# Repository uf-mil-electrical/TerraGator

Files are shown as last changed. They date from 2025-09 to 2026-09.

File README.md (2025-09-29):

# TerraGator Rover
This repo should contain all files related to TerraGator ~~ReptileRover~~, including all Electrical, Mechanical (if applicable), and Software files.

Important links
- [TerraGator Team document](https://docs.google.com/document/d/1ea5GAN0c3F9gpOd2iORHwbelWknOrgWVgWwZqf3MmRY/edit?usp=sharing) <br>
- [Russell's brainstorming document for all things TerraGator](https://docs.google.com/document/d/1PND_ZT07X8xPTkg0Q3CSGb8W5NNpszSxxChMyouKteI/edit?usp=sharing)

Thanks!

## Folders
`PCBs` contain PCBs designed for the rover. Deprecated PCBs should be stored in the *Deprecated or Legacy* folder.

`Deprecated or Legacy` contains old documentation, software, CAD, and images.

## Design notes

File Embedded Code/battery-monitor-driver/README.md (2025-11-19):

## Battery Monitor Board Driver

The following code contains the means for operating TerraGator's Battery Monitor Board. The current project structure is listed below:

``` pgssql
battery_monitor/
│
├── CMakeLists.txt
├── pico_sdk_import.cmake
│
├── src/
│   ├── main.c
│   ├── board_config.c / board_config.h
│   ├── drivers/
│   │   ├── current_sens.c / current_sens.h
│   │   ├── led.c / led.h
│   │   ├── rpi5_comm.c / rpi5_comm.h
│   │   ├── sseg.c / sseg.h
│   │   └── voltage_sens.c / voltage_sens.h
│   └── 
└── 
```
For more detailed information on driver, visit [this MILwiki link](https://milwiki.cbrxyz.com/wiki/Battery_Monitor_Board_V1_Driver)

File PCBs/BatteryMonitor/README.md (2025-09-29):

This is where I'd put my BatteryMonitor files.... *if i had any!?!?!?!*

^^About that^^, I've started working on the pcb design for this board. ye. - Russell

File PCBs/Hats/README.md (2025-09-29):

# Pi hat and motor hats super cool

We'll end up with 4 hats (one for the PI, one for each motor driver).

While EN1 and EN2 aren't routed to anything on the Pi-hat, they should still be input/output from the motor hat

# Here's a motor legend
legend for dc hat

# Here's a Pi legend
legend for dc hat

# Here's the general wiring spec (you'll make 4 hats and these will be the connections in-between them)
legend for dc hat

EN1 and EN2 aren't connected to the PI hat but should still be exposed by the hats (just like every other pin)

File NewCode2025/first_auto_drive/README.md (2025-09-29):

# what is this ros pkg

- wheel drivers (topic)
- sonar drivers (topic)
- IMU driver (topic and server)
- main\_node (listener and client)

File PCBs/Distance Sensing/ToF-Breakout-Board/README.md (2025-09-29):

## Overview

The time-of-flight (ToF) breakout board is a small PCB that can be used for collision detection on TerraGator. The plan is to mount one all four sides of TerraGator so that we can minimize collisions between objects and the rover. 

## Documentation

For more information on the ToF sensor used (VL53L1X) and ToF breakout board can be found on the MIL wiki.

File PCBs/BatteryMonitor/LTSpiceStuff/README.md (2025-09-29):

### what does the battery monitor board do???

Not much! It monitors the batteries voltage and will blink an indicator when the 
battery gets too low (so we can change/re-charge it)

It might be worth adding temperature sensors/monitors as a feature in the future.
I don't think overheating is really an issue but idrk.

### what does the battery monitor board look like in LTSpice

A mess!



Here's an image of the LTSpice schematic

#### how it works

- left most thing
    - the leftmost thing is VBat (24V)
    - it's also +5V and -5V (you get them from a buck converter or something)
- second to the left is an op-amp circuit
    - this op-amp has a gain of ~$\frac{5}{24}$
    - this has the annoying side affect of inverting the signal
- inverting stage
    - literally just an op-amp that (un)inverts the signal 
- output stage
    - what should we do???
    - Depends:
        - led indicator
        - digital signal for PI or uP
        - analog voltage that indicates strength of battery

# TODOS

lowk this spice sim assumes that the battery can vary from
0-24V which is 100% cap!

the battery can vary between 22.4V and 24V

22.4V is 0%
24V is 100% 

(and everything in between is linear)

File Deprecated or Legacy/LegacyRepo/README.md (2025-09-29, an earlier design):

Repo for parts for the MIL Rover

Old Rover CAD Screenshot

contact: adammcaleer@ufl.edu

## Project Architecture
Iamge overview

### Finished tasks
Firmware has somewhat shifted away from a build system using wiringPI as a HAL for c++ - have moved towards a build system for assembly and C for performance. <br>
The basics of the drivers for PWM are done under the c_drivers directory, and drivers for an IMU and BME280 are available under the main branch now.<br>
We have now also added configurations for sonar in the form of a kernel interrupt - this being done once again in hopes of better performance<br>
<br>
Our high level software team has finished configuring ROS for our external computer nodes, and have dived into the details of ROS through toturials.<br>
<br>
Additionally, the team has dived into the battery monitor board design, and details of the future voltage dividing procedure.<br>
<br>
The team has also spent a great deal of time researching and buying parts. Included in the documentation directory are details on that procedure, especailly for the motor selection<br>
<br>
We encourage you to explore the repo and read the subdirectory README's and the different available documentation

## Bugs
Firmware bugs are as follows: PWM through DMA drivers needs to become a persistant object to capture memory leaks - otherwise causes issues when run multiple times<br>
Our sonar modules work independently, but need some kind of daisychaning or internal delays to prevent interference with one another.

## Set up to run:
1. Load the gpio_interface module for PWM
```
cd /Mars-Rover/firmware/kernel_modules/
sudo insmod gpio_interface.ko
```

## Installation:
1. Clone our repo
```
git clone https://github.com/kberon/Mars-Rover.git
```
2. Instantiate the kernel modules on start up
```
sudo nano /etc/systemd/system/load_custom_modules.service
```
In that file write:
```
[Unit]
Description=Load Custom Sonar Kernel Modules
After=network.target

[Service]
Type=oneshot
ExecStart=/sbin/insmod /home/raspberry/Mars-Rover/firmware/sonar_1/sonar_1.ko
ExecStart=/sbin/insmod /home/raspberry/Mars-Rover/firmware/sonar_2/sonar_2.ko
ExecStart=/sbin/insmod /home/raspberry/Mars-Rover/firmware/sonar_3/sonar_3.ko
RemainAfterExit=yes

[Install]
WantedBy=multi-user.target
```
Save the file and run the following commands:
```
sudo systemctl daemon-reload
sudo systemctl enable load_custom_modules.service
```

3. For the sensor setup, we will need to install the WiringPi library
```
cd Mars-Rover/firmware/drivers
git clone https://github.com/WiringPi/WiringPi.git
cd WiringPi
./build debian
sudo dpkg -i debian-template/wiringpi_3.10_arm64.deb
```
4. Docker setup
Get the install script:
```
curl -fsSL https://get.docker.com -o get-docker.sh
chmod +x get-docker.sh
```
Remove an existing docker installations with:
```
sudo apt-get purge docker-ce docker-ce-cli containerd.io -y
```
Run the script:
```
./get-docker.sh
```
Fix permissions:
```
sudo usermod -aG docker pi
sudo systemctl unmask docker
sudo chmod 666 /var/run/docker.sock
```
Install docker-compose:
```
pip3 -v install docker-compose
```
Start and reboot Docker:
```
sudo systemctl start docker
sudo init 6
```   
6. To run our camera + sensors executable:
```
sudo apt-get install libgtk-3-dev
sudo apt-get install libopencv-dev
sudo apt install python3-opencv
```

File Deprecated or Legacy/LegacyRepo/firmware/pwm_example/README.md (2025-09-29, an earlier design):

Try running make in this directory.<br>

If it doesn't work/it cannot find the directory then do the following:<br>
**NOTE if any of the below steps fail, go to IF STILL DOESN'T WORK section, do not continue running the next commands NOTE**<br>
cd WiringPi<br>
rm wiringpi_3.2_armhf.deb<br>
./build debian<br>
mv wiringpi_3.2_armhf.deb .<br>
sudo apt install ./wiringpi_3.2_armhf.deb<br>
<br>
<br>
<br>
IF IT STILL DOESN'T WORK<br>
return to firware directory<br>
rm -r WiringPi<br>
git clone https://github.com/WiringPi/WiringPi.git <br>
cd WiringPi<br>
./build debian<br>
mv debian-template/wiringpi_3.2_armhf.deb .<br>
sudo apt install ./wiringpi_3.2_armhf.deb <br>

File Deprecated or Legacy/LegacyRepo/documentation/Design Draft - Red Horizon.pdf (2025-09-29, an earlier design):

### Design Revision CEN3907C: Senior Design for Computer Engineering

Red Horizon Team
Kayleigh Beron, Andrea Chacon, Morgan Cobb, Kayla Dunnuck, Quintin Lopez-Scarim Machine Intelligence Lab - University of Florida

Table of Contents

Introduction
The Red Horizon project aims to develop a prototype of a Mars rover, integrating advanced features to enhance its autonomy and functionality.

Purpose/Need

The purpose of the Red Horizon project lies in providing an educational and research platform for exploring the capabilities of machine intelligence in autonomous robotic systems. This replica serves as a valuable tool for students, researchers, and educators at the Machine Intelligence Lab to study and experiment with autonomous navigation, object detection, and sensor integration. By simulating the functionalities of a Mars rover, the project fulfills the need for practical hands-on experience in developing and deploying intelligent robotic systems.

Red Horizon will be used by the Machine Intelligence Lab to show off the kinds of autonomous projects students of all ages could work on if they choose to pursue STEM and join MIL. However, there are many possible applications as well, as its mechanical chassis design and motor system allow for movement across all kinds of terrains. It’s strong ability to go over things in all kinds of terrain, make it possible to be used in emergency situations, where it could use the camera to detect victims in areas of natural disasters or cramped spaces where it would be too dangerous to send a person without confirmation of victims.

Domain & Prior Art

The Red Horizon project operates within the field of autonomous robotics and control systems. While there have been significant achievements in this domain, including successful Mars rover missions conducted by various countries, our project aims to recreate this to not only help Machine Intelligence Lab bring a stronger attraction to STEM education with something of great historical significance, but to create something that could be applied in emergencies.

Some prior art would be the original Mars Rover that we would be imitating from, as the wheels and mechanical system are nearly identical. As for educational prior art, Makeblock creates “mBots” that are robots that can easily be built and programmed by young teens, to get introduced to the basics of robotics and allow young engineers to both learn and play with the robot they’ve created. The FIRST Competition is also a robotics competition aimed at middle schoolers and high schoolers of different levels to create a robot with autonomous and telemetry modes with computer vision, that allow young kids to learn about the basics of robotics and gain interest.

Differentiation

As for how Red Horizon will be different, Red Horizon will be more complex than those educational tools like FIRST and mBots, as it is a project that wouldn’t be built by the young kids it is aiming to inspire as it would be too difficult for their level. It is a chance for those kids who are working in FIRST Robotics, to see a more complex project and the real world applications of what they could be working on. This is a project we could bring to local schools with FIRST robotics teams and allow them to play with it while seeing how they can apply robotics outside of a high-school competition.

Impact & Risk Assessment

The impact of the Red Horizon project extends primarily to the educational and research domains within the university community. By providing a hands-on learning experience, the project enhances students' understanding of machine intelligence, robotics, and computer engineering.
The project also raises ethical and privacy concerns, particularly regarding the use of onboard cameras for object detection and navigation. The potential for unintended surveillance or privacy breaches requires careful consideration and implementation of privacy safeguards. As for how we will address this, we will ensure that the robot cannot leave MIL room by trying to make a docking station for it, and ensure the camera is at an angle it can only see directly in-front from a low height. The controllers for it will be kept by Dr. Schwartz as well.

Drawbacks and Limitations

While creating a Mars rover replica like Red Horizon for educational purposes is exciting, it comes with several drawbacks and limitations. Firstly, reliance on computer vision for navigation may be prone to errors in identifying colors and shapes accurately, especially in challenging environments. Additionally, the rover's autonomy may lead to unpredictable behavior, potentially causing collisions or getting stuck in obstacles. Moreover, replicating the complex terrain and environmental conditions of Mars accurately can be difficult, limiting the realism and educational value of the experience. Overall however, these limitations shouldn’t be too large to affect the educational experience.

Statement of Work

By the pre-alpha build (03/27) the Red Horizon team plans to have drivers for the Motors and the controller, along with our high level ROS (Robot Operating System) environment. For the drivers we plan to use C++,C, and potentially some assembly for speed and efficiency. C++ and C will be the default for most drivers, and assembly will be used for some reach goal by utilizing some cutting edge communication protocols. For the specific communication protocols we plan to use for each peripheral please see either the tables below, or the diagram included in the systems section. We will use Cmake as our build system since it meshes well with C++, C, assembly, and ROS. The motor board and kill board will be completed and most parts should be ordered and will continue until the end of the alpha build. We also hope to order sonar kits, and to have a better foundational understanding of the current mechanical state of the Red Horizon.

By the completion of our prototype (04/16) development, we hope to have drivers for the gyroscope, camera, and interfacing with our external computer. Once again, we will be utilizing C++,C, and assembly for that, along with Cmake as our build system. The voltage divider board and battery monitor board will be completed and tested to ensure functionality. Some of our secondary features that we hope to get done include drivers for an accelerometer, and patching up any mechanical issues.

As for our alpha build/demo (08/27) we plan to have attached sonar with drivers in C and C++ using Cmake, and hope to utilize daisy-chaining to increase their accuracy. With those sonar attachments come more information that we can use to increase autonomy, which we hope to have at a sufficient level to roam on its own at this point without destroying itself. . Bluetooth and wifi will also be connected to the controllers to the kill board and raspberry pi. LCD output will be created and tested to ensure data from the screen outputs all current data correctly.

Pre-Alpha build

Core features | Done by: | Secondary features | Timeline (Starting March 11th)
Controller Drivers (wifi) | Quintin and Andrea | Order sonar kits/start researching how to daisy chain them | Week 2
Motor/DAC Drivers | Quintin and Andrea | | Week 3
Configure ROS | Morgan | | Week 1-2
Begin teleop code | Morgan and Kayla | | Week 2

Determine the current mechanical state of Red Horizon | Quintin | Week 1
Motor and Kill Board | Kayleigh and Kayla | Weeks 1-3
Initialize Raspberry Pi | Andrea | Weeks 1-3

Prototype

Core features | Done by: | Secondary features | Timeline (Week 4 starting 04/01/2024)
Motors attached with minimal functionality | Everyone | Accelerometer drivers | Weeks 4-6
Gyroscope drivers (I2C) | Quintin | Mechanical fixes | Week 4-5
UI for data/connectivity with computer | Morgan and Kayla | | Week 4
Begin high level data analysis (basic autonomy) | Morgan and Kayla | | Week 5-6
Add camera with base drivers (USB) | Andrea | | Week 6
Configure LCD to Raspberry Pi (SPI) | Andrea | | Week 4-5
Configure remote controller (WIFI) | Andrea and Kayleigh | | Week 5-6
Voltage Divider and Battery Monitor Board | Kayleigh and Kayla | | Week 4-6

Alpha build/demo

Core features | Done by: | Secondary features | Timeline (Continuing on starting 08/12/2024 with some work done over summer)
Attach functioning sonar | Quintin and Andrea | Path mapping with an accelerometer | Week 7-8
Basic autonomy through high level interactions finished | Quintin and Andrea | Mechanical fixes | Week 9-10
Finish part ordering | Kayleigh | | Week 7
Start testing and integration | Everyone | | Week 7-10

Deliverable Artifacts

We intend to deliver the software for the control, as well as drivers/libraries created for the firmware in a github repository. Documentation in the form of jupyter notebooks for these drivers will be provided. Additionally, we will deliver the PCB’s used for the kill board, voltage divider board, motors board, and battery monitor board with their schematics. The final product will be all of these features combined onto the working rover, and delivered to the faculty supervisor, to be used for future research lab demos.

As for how this will be maintained for long-term use there are several plans. The robot will stay in the Machine Intelligence Lab, and the controllers will be kept by Dr. Schwartz. We will provide the CUI to Dr. Schwartz, and keep it on one of the computers in the MIL lab. On one of the computers in the MIL lab, students should just receive the controllers by Dr. Schwartz, run the .exe file on the MIL computer to open the CUI, and once the controllers are connected and the CUI is booted establishing connection to the rover, students should be free to use the rover around the room as pleased. This software will also be available on one of the MIL laptops that can be used at outreach events with local schools for educational purposes, and documentation will be provided on how to use and how to fix some possible issues. Lastly, we will provide a final paper that describes how it works that can be studied by any MIL member.

Mockups
Interfaces

The main interface of this project would be the Bluetooth Logitech Controllers and the LCD Screen. The main inputs from humans come from the kill button (a large physical button on the exterior of the robot to emergency kill), as well as the bluetooth controllers that would change the rover from autonomous to teleop mode (driving by human control) by moving a joystick, and reset it based on a button. We could possibly also try a phone app, not sure if we will implement that yet. The LCD screen would display the status of everything (kill/not kill mode, teleop or autonomous mode, temperature, humidity, altitude, orientation, and if detecting anything on the sensors, all based on the different sensors).
Below is a possible LCD Screen output:

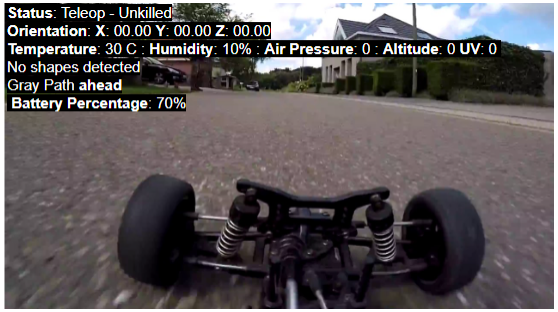
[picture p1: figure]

Figure 1: Potential LCD Screen output Below is a possible remote controller mapping. The soil test is specifically for activating the soil test state that would push a servo stick into the dirt, and output the results from it into the LCD display.

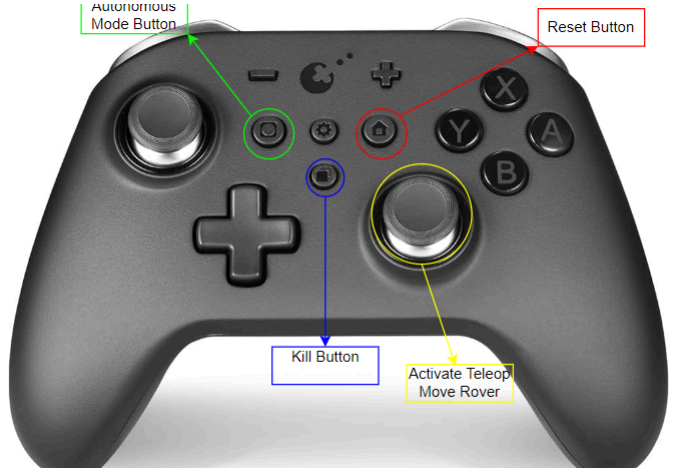
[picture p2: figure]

Figure 2: Remote Controller Map

Systems

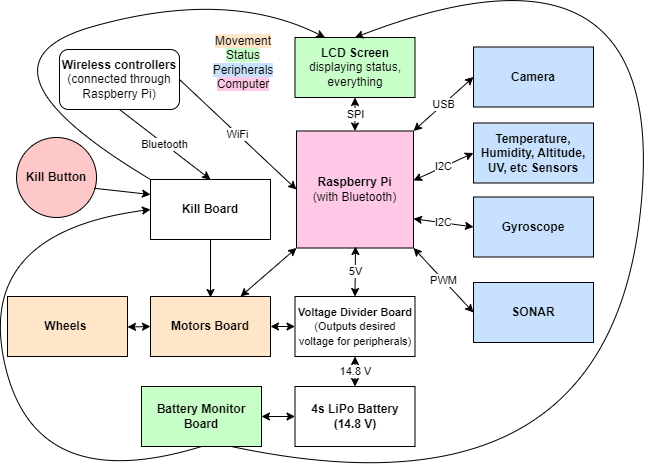
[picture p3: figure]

Above is the general hardware system diagram for our project. Below is the block diagram for the high-level software (computer vision) algorithm. Our main computer will be a Raspberry Pi with Bluetooth functionality that would connect via Bluetooth to the Kill Board (kills all motors/servos when necessary).

We would have a motor system with different motors for each wheel, (possibly mecanum wheels), an arm system involving a servo that just sticks a soil quality sensor into the dirt, and output displayed on the LCD. We would also have a camera connected to the computer searching for shapes and colors (e.g: red circle detected in the distance). Lastly there should be a status system for killed, unkilled, autonomous, teleop, etc.

Networking

There are several necessary communication protocols to fully implement our rover. We would use Serial Peripheral Interface (SPI) communication from our Pi to the screen, to be able to display our sensor and critical information quickly. Additionally, the sensors will use Inter-Integrated Circuits (I2C) or SPI - depending on how critical the data transfers are, as well as the physical location of the hardware components. Additionally, we will use Pulse Width Modulation (PWM) to communicate with the sonar sensors, encoding analog signals into digital signals.

In order to communicate with our Pi from our controller, we will use a CUI that will send instructions to the Pi via Wifi for high data transfer, wide coverage range, and flexibility. We will also use bluetooth or wifi to communicate with the kill board.

Storyboards

The LCD, which is the biggest output, will just look like this most of the time, with the values not in bold, changing every millisecond.

Storyboard example:

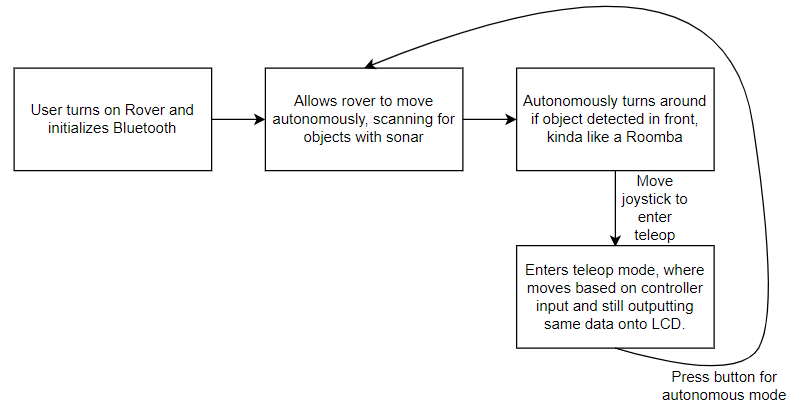
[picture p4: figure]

Draft Schematics

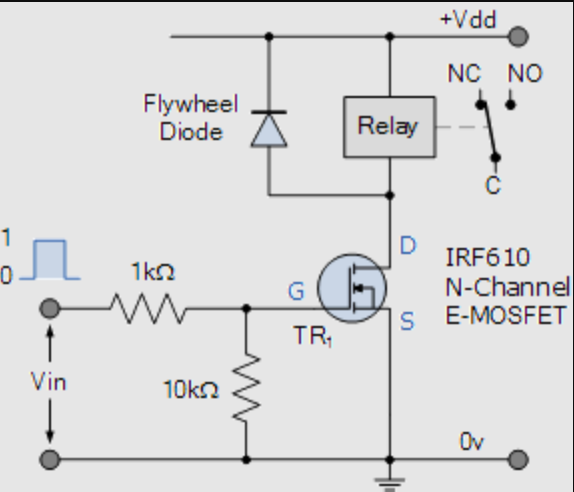
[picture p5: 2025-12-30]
PCBs/Safety Board V0/relay control circuit.png

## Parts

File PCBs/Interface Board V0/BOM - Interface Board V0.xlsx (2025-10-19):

Type | Designator(s) | Qty | Value | Detailed Description | Part Number | Size | Unit Price | Total Price | Vendor
Capacitor | C11, C12, C15, C16, C17, C18, C19, C20, C21, C22, C23, C24, C25, C26, C27, C28, C29, C30, C31, C32 | 20 | 100nF | 0.1 µF ±10% 50V Ceramic Capacitor X7R 0805 (2012 Metric) | C0805C104K5RACTU | 0805 | $0.16 | $3.20 | DigiKey
Capacitor | C1, C2, C6, C7 | 4 | 180uF | 180 µF 50 V Aluminum Electrolytic Capacitors Radial, Can 2000 Hrs @ 105°C | EEU-FC1H181L | 8mm dia | $0.72 | $2.88 | DigiKey
Capacitor | C3, C4, C5, C8, C9, C10 | 6 | 15uF | 15 µF 160 V Aluminum Electrolytic Capacitors Radial, Can 15000 Hrs @ 105°C | 160LLE15MEFC8X11.5 | 8mm dia | $0.52 | $3.12 | DigiKey
Capacitor | C13, C14 | 1 | 0.47uF | 0.47 µF ±10% 50V Ceramic Capacitor X7R 0805 (2012 Metric) | 160LLE15MEFC8X11.5 | 0805 | $0.21 | $0.21 | DigiKey | Total: | $66.32
Connector | X2 | 1 |  | USB-A (USB TYPE-A) Receptacle Connector 4 Position Through Hole, Right Angle | USB-A1HSW6 | 0805 | $0.50 | $0.50 | DigiKey
Connector | X3, X5, X6, X7 | 4 |  | 6 Pin Screw Terminal, Power Tap M3 Through Hole | 7461057 | 0805 | $2.31 | $9.24 | DigiKey
Connector | X4 | 1 |  | 4 Position Wire to Board Terminal Block Horizontal with Board 0.197" (5.00mm) Through Hole | TB001-500-04BE |  | $0.70 | $0.70 | DigiKey
Connector | X8 | 1 |  | 6pin 2.54mm JST |  |  |  | $0.00 | Lab
Connector | X9 | 1 |  | 2pin 2.54mm JST |  |  |  | $0.00 | Lab
Connector | H26 | 1 |  | Connector Header Through Hole, Right Angle 14 position 0.100" (2.54mm) | 22052141 |  | $1.13 | $1.13 | DigiKey
Connector | H25 | 1 |  | 2x14 Headers |  |  |  | $0.00 | Lab
Connector | H1, H21, H22, H23, H24 | 4 |  | Connector Header Through Hole 3 position 0.100" (2.54mm) | 070543-0037 |  | $0.78 | $3.12 | DigiKey
Connector | H18, H19, H20 | 3 |  | Connector Header Through Hole 10 position 0.100" (2.54mm) | BHR-10-VUA |  | $0.28 | $0.84 | DigiKey
Connector | H8, H9, H10, H11, H12, H13, H14, H15, H16, H17 | 10 |  | Connector Header Through Hole 4 position 0.100" (2.54mm) | 70543-0003 |  | $0.85 | $8.50 | DigiKey
Connector | H3, H4, H5, H6, H7 | 5 |  | Connector Header Through Hole 6 position 0.079" (2.00mm) | 35362-0650 |  | $0.35 | $1.75 | DigiKey
Connector | Mount1, Mount2, Mount3, Mount4 | 4 |  | M3 Mounting Bolts |  |  |  | $0.00 | Lab
Connector | X1 | 1 |  | 40 Position Receptacle Connector 0.100" (2.54mm) Through Hole, Right Angle Gold | XG4H-4034 |  | $5.27 | $5.27 | DigiKey
Connector | Radio1 | 1 |  | 16 Position Receptacle Connector 0.100" (2.54mm) Through Hole, Right Angle Gold | 89883-308LF |  | $1.56 | $1.56 | DigiKey
Connector | Mates with 070543-0037 | 4 |  | 3 Rectangular Connectors - Housings Receptacle Black 0.100" (2.54mm) | 50579403 |  | $0.21 | $0.84 | DigiKey
Connector | Mates with 70543-0003 | 10 |  | 4 Rectangular Connectors - Housings Receptacle Black 0.100" (2.54mm) | 50579404 |  | $0.26 | $2.60 | DigiKey
Device | Radio1 | 1 |  | RFDx900 Modem |  |  |  | $0.00 | Lab
Device | X1 | 1 |  | Raspberry Pi 5 |  |  |  | $0.00 | Lab
Diode | D1, D2 | 2 |  | Diode 45 V 6A Surface Mount TO-263AB (D2PAK) | VS-6TQ045S-M3 | TO263AB | $0.76 | $1.52 | DigiKey
Inductor | L1, L2 | 2 | 10uH | 10 µH Shielded Molded Inductor 5 A 43mOhm Max Nonstandard | ASPI-5050LR-100M-T | 6.00mm x 5.70mm | $1.06 | $2.12 | DigiKey
Regulator | U1 | 1 | 5V, 5A | Buck Switching Regulator IC Positive Fixed 5V 1 Output 5A TO-263-8, D2PAK (7 Leads + Tab), TO-263CA | LM2678SX-5.0/NOPB | TO263 | $6.99 | $6.99 | DigiKey
Regulator | U2 | 1 | 3V3, 5A | Buck Switching Regulator IC Positive Fixed 3.3V 1 Output 5A TO-263-8, D2PAK (7 Leads + Tab), TO-263CA | LM2678SX-3.3/NOPB | TO263 | $6.99 | $6.99 | DigiKey
Ribbon cable | Mates with BHR-10-VUA | 3 |  | 10 Position Cable Assembly Rectangular Socket to Socket 0.500' (152.40mm, 6.00") | H3CCH-1006M |  | $1.08 | $3.24 | DigiKey

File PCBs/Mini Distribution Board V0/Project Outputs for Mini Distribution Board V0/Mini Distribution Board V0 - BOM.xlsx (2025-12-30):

Line # | Name | Description | Designator | Quantity | Manufacturer 1 | Manufacturer Part Number 1 | Manufacturer Lifecycle 1 | Supplier 1 | Supplier Part Number 1 | Supplier Unit Price 1 | Supplier Subtotal 1
 | [Cap] SMD Nonpolarized |  | C1, C2 | 2 | Yageo Group | CC0603KRX7R7BB104 | Volume Production | DigiKey | 311-1088-6-ND | 0.006 | 0.06
 | SMD Polarized |  | C3 | 1 | Panasonic | EEE-FK1A681P | Volume Production | DigiKey | PCE3781CT-ND | 0.88 | 0.88
 | SMD Polarized |  | C4 | 1 | Nichicon | UCM0J221MCL1GS | Volume Production | DigiKey | 493-17593-1-ND | 0.47 | 0.47
 | Schottky | Generic | D1 | 1 | Diodes Inc. | B530C-13-F | Volume Production | DigiKey | B530C-FDICT-ND | 0.62 | 0.62
 | [PTC] 500mA Trip | MF-MSMF050-2 | F1 | 1 | Bourns | MF-MSMF050-2 | Volume Production | DigiKey | MF-MSMF050-2DKR-ND | 0.36 | 0.36
 | Right-Angle |  | F2 | 1 | Keystone | 3549-2 | Volume Production | DigiKey | 36-3549-2-ND | 1.23 | 1.23
 | 1x4 Male | 70543-0003 Mates with 005057-9404 | H1, H2 | 2 | Molex | 70543-0003 | Volume Production | Avnet | 0705430003 | 0.42149 | 0.84298
 | 1x2 Male | 0705430036 Mates with 0050579402 | H3, H4 | 2 | Molex | 50-57-9402 | Volume Production | DigiKey | WM2900-ND | 0.31 | 0.62
 | SMD Inductor |  | L1 | 1 | TDK | MLZ2012M330WT000 | Volume Production | DigiKey | 445-6399-1-ND | 0.1 | 0.1
 | 652-MH2029-300Y | 652-MH2029-300Y | L2 | 1 | Bourns | MH2029-300Y | Volume Production | DigiKey | MH2029-300YCT-ND | 0.1 | 0.1
 | PMV48XP | PMV48XP | Q1 | 1 | Nexperia | PMV48XPA2R | Volume Production | DigiKey | 1727-PMV48XPA2RCT-ND | 0.5 | 0.5
 | [Res] SMD Resistor | Generic | R1, R2 | 2 | Yageo Group | RC0603FR-0710KL | Volume Production | DigiKey | 311-10.0KHRDKR-ND | 0.006 | 0.06
 | SPDT |  | S1 | 1 | EAO Switch | 09.03290.01 | Volume Production | DigiKey | 1948-1087-ND | 1.67 | 1.67
 | 3.3V 3A | 3A | U1 | 1 | Texas Instruments | LM2596SX-3.3/NOPB | Volume Production | DigiKey | LM2596SX-3.3/NOPBCT-ND | 6 | 6
 | Comparator | LMV358IDGKR | U2 | 1 | Texas Instruments | LMV358IDGKR | Volume Production | DigiKey | 296-13455-1-ND | 0.38 | 0.38
 | 2pin Screw Terminal |  | X1 | 1 | Same Sky | TB002-500-02BE | Volume Production | DigiKey | 102-6145-ND | 0.4 | 0.4

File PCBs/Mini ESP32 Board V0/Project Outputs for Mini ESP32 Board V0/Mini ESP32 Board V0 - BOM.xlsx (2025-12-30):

Line # | Name | Description | Designator | Quantity | Manufacturer 1 | Manufacturer Part Number 1 | Manufacturer Lifecycle 1 | Supplier 1 | Supplier Part Number 1 | Supplier Unit Price 1 | Supplier Subtotal 1
 | RP-SMA 50-Ohm | PCB.RPSMAFRA.HT | A1 | 1 | Taoglas | PCB.RPSMAFRA.HT | Unknown | DigiKey | 931-1360-ND | 3.59 | 3.59
 | SMD Nonpolarized |  | C1, C2 | 2 | Cal-Chip Electronics | CHV0603N2501R2BCT | Unknown | DigiKey | 4713-CHV0603N2501R2BCT-ND | 0.22 | 0.44
 | [Cap] SMD Nonpolarized |  | C3, C13, C14, C15, C16 | 5 | Yageo Group | CC0603KRX7R7BB104 | Volume Production | DigiKey | 311-1088-6-ND | 0.006 | 0.06
 | SMD Nonpolarized |  | C4, C5 | 2 | Yageo Group | CC0603DRNPO9BN6R0 | Volume Production | DigiKey | 311-1055-1-ND | 0.1 | 0.2
 | SMD Nonpolarized |  | C6, C7, C10, C17, C18 | 5 | Samsung Electro-Mechanics | CL10B105MO8NNWC | Volume Production | DigiKey | 1276-6524-1-ND | 0.006 | 0.06
 | SMD Nonpolarized |  | C8 | 1 | Murata | GRM1885C1H101JA01D | Not Recommended for New Design | DigiKey | 490-1427-1-ND | 0.08 | 0.08
 | SMD Nonpolarized |  | C9 | 1 | TAIYO YUDEN | LMK107BBJ106MALT | Volume Production | DigiKey | 587-3258-1-ND | 0.08 | 0.08
 | SMD Nonpolarized |  | C11, C12 | 2 | KYOCERA AVX | 600S1R8BT250XT4K | Volume Production | DigiKey | 478-600S1R8BT250XT4KCT-ND | 1.38 | 2.76
 | 1x4 Male | 70543-0003 Mates with 005057-9404 | H1 | 1 | Molex | 70543-0003 | Volume Production | Avnet | 0705430003 | 0.42149 | 0.42149
 | 1x3 Male | 070543-0037 Mates with 005057-9403 | H2 | 1 | Molex | 50-57-9403 | Volume Production | DigiKey | WM2901-ND | 0.22 | 0.22
 | SMD Inductor |  | L1 | 1 | Wurth Elektronik | 7447860027G | Unknown | DigiKey | 732-7447860027GCT-ND | 0.1 | 0.1
 | SMD Inductor |  | L2 | 1 | Murata | LQW18AS2N0J00D | Volume Production | DigiKey | 490-LQW18AS2N0J00DCT-ND | 0.11 | 0.11
 | 652-MH2029-300Y | 652-MH2029-300Y | L3 | 1 | Bourns | MH2029-300Y | Volume Production | DigiKey | MH2029-300YCT-ND | 0.1 | 0.1
 | [Res] SMD Resistor | Generic | R1, R2 | 2 | Vishay | MCT06030C2709FP500 | Volume Production | DigiKey | 749-1631-1-ND | 0.1 | 0.2
 | [Res] SMD Resistor | Generic | R3, R4 | 2 | Yageo Group | RC0603FR-075K1L | Volume Production | DigiKey | 311-5.10KHRDKR-ND | 0.007 | 0.07
 | [Res] SMD Resistor | Generic | R5 | 1 | Yageo Group | RT0603BRD071ML | Volume Production | DigiKey | YAG4498CT-ND | 0.1 | 0.1
 | [Res] SMD Resistor | Generic | R6, R7 | 2 | Yageo Group | RC0603FR-0710KL | Volume Production | DigiKey | 311-10.0KHRCT-ND | 0.006 | 0.06
 | [Res] SMD Resistor | Generic | R8, R9 | 2 | Panasonic | ERA3ARB202V | Volume Production | DigiKey | P2.0KBDCT-ND | 0.35 | 0.7
 | ESP32-S2FN4R2 |  | U1 | 1 | Espressif Systems | ESP32-S2FN4R2 | Unknown | DigiKey | 1965-ESP32-S2FN4R2CT-ND | 2.94 | 2.94
 | W25Q128JVS | W25Q128JVSIQ TR | U2 | 1 | Winbond | W25Q128JVSIQ TR | Unknown | DigiKey | 256-W25Q128JVSIQTRCT-ND | 2.13 | 2.13
 | USB-C |  | X1 | 1 | JAE Electronics | DX07S024JA1R1300 | Volume Production | DigiKey | 670-3104-1-ND | 2.1 | 2.1
 | 40MHz Crystal | CX2016DB40000D0FLJCC | Y1 | 1 | KYOCERA AVX | CX2016DB40000D0FLJCC | Unknown | DigiKey | 478-CX2016DB40000D0FLJCCDKR-ND | 0.84 | 0.84

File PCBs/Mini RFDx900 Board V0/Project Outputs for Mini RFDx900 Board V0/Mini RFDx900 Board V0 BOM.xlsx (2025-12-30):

Line # | Name | Description | Designator | Quantity | Manufacturer 1 | Manufacturer Part Number 1 | Manufacturer Lifecycle 1 | Supplier 1 | Supplier Part Number 1 | Supplier Unit Price 1 | Supplier Subtotal 1
 | [Cap] SMD Nonpolarized |  | C1, C2, C3 | 3 | Yageo Group | CC0603KRX7R7BB104 | Volume Production | DigiKey | 311-1088-6-ND | 0.006 | 0.06
 | SMD LED | Generic | D1, D2 | 2 | Harvatek | B1701UY--20D000214U1930 | Unknown | DigiKey | 3147-B1701UY--20D000214U1930CT-ND | 0.1 | 0.2
 | 1x2 Male | 0705430036 Mates with 0050579402 | H1 | 1 | Molex | 50-57-9402 | Volume Production | DigiKey | WM2900-ND | 0.31 | 0.31
 | 652-MH2029-300Y | 652-MH2029-300Y | L1 | 1 | Bourns | MH2029-300Y | Volume Production | DigiKey | MH2029-300YCT-ND | 0.1 | 0.1
 | [XOSC] SMD 12MHz |  | O1 | 1 | Murata | CSTNE12M0GH5L000R0 | Volume Production | DigiKey | 490-17947-1-ND | 0.32 | 0.32
 | [Res] SMD Resistor | Generic | R1, R2 | 2 | Stackpole Electronics | RMCF0603FT1K00 | Volume Production | DigiKey | RMCF0603FT1K00DKR-ND | 0.007 | 0.07
 | [Res] SMD Resistor | Generic | R3 | 1 | Yageo Group | RC0603FR-0710KL | Volume Production | DigiKey | 311-10.0KHRDKR-ND | 0.1 | 0.1
 | [Res] SMD Resistor | Generic | R4, R5 | 2 | Vishay | MCT06030C2709FP500 | Volume Production | DigiKey | 749-1631-1-ND | 0.1 | 0.2
 | [Res] SMD Resistor | Generic | R6, R7 | 2 | Yageo Group | RC0603FR-075K1L | Volume Production | DigiKey | 311-5.10KHRDKR-ND | 0.007 | 0.07
 | RFDX900 | RFDX900 Long-Range RF Module | Radio1 | 1 | Amphenol Communications Solutions | 71609-308LF | Volume Production | DigiKey | 609-71609-308LF-ND | 2.71 | 2.71
 | USB-UART Bridge | MCP2200T-I/SO | U1 | 1 | Microchip | MCP2200T-I/SO | Volume Production | DigiKey | MCP2200T-I/SOCT-ND | 2.61 | 2.61
 | USB-C |  | X1 | 1 | JAE Electronics | DX07S024JA1R1300 | Volume Production | DigiKey | 670-3104-1-ND | 2.1 | 2.1

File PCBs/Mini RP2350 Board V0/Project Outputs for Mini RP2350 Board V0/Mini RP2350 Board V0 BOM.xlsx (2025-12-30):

Line # | Name | Description | Designator | Quantity | Manufacturer 1 | Manufacturer Part Number 1 | Manufacturer Lifecycle 1 | Supplier 1 | Supplier Part Number 1 | Supplier Unit Price 1 | Supplier Subtotal 1
 | [Cap] SMD Nonpolarized |  | C1, C4, C5, C6, C7, C8, C9, C10, C11, C15, C16, C17, C18, C19, C21, C22, C23, C24, C25, C26, C27 | 21 | Yageo Group | CC0603KRX7R7BB104 | Volume Production | DigiKey | 311-1088-6-ND | 0.006 | 0.126
 | [Cap] SMD Nonpolarized |  | C2, C3 | 2 | Murata | GCM1885C2A150FA16D | Volume Production | DigiKey | 490-16416-1-ND | 0.14 | 0.28
 | [Cap] SMD Nonpolarized |  | C12, C13, C14, C20 | 4 | Murata | GRM188R61E475KE11D | Volume Production | DigiKey | 490-7203-1-ND | 0.08 | 0.32
 | SMD LED | Generic | D1 | 1 | Osram Opto | LG R971-KN-1-0-20-R18 | Unknown | DigiKey | 475-LGR971-KN-1CT-ND | 0.15 | 0.15
 | SMD LED | Generic | D2 | 1 | Osram | LY R976-PS-36-0-20-R18 | Unknown | DigiKey | 475-LYR976-PS-36-0-20-R18CT-ND | 0.15 | 0.15
 | SMD LED | Generic | D3 | 1 | Osram Opto | LS R976-NR-1-0-20-R18 | Unknown | DigiKey | 475-LSR976-NR-1CT-ND | 0.15 | 0.15
 | SMD LED | Generic | D4, D5 | 2 | Wurth Elektronik | 150080BS75000 | Unknown | DigiKey | 732-4982-1-ND | 0.19 | 0.38
 | 2x5 Shrouded | BHR-10-VUA | H1, H2, H3 | 3 | Adam Tech | BHR-10-VUA | Volume Production | DigiKey | 2057-BHR-10-VUA-ND | 0.28 | 0.84
 | 1x3 Male | 070543-0037 Mates with 005057-9403 | H4, H6, H7, H8, H10 | 5 | Molex | 50-57-9403 | Volume Production | DigiKey | WM2901-ND | 0.22 | 1.1
 | 1x2 Male | 0705430036 Mates with 0050579402 | H5 | 1 | Molex | 50-57-9402 | Volume Production | DigiKey | WM2900-ND | 0.31 | 0.31
 | [Header] Shrouded 1x6 Male | 0705430005 Mates with 0050579406 | H9, H12 | 2 | Molex | 50-57-9406 | Volume Production | DigiKey | WM2904-ND | 0.4 | 0.8
 | 1x4 Male | 70543-0003 Mates with 005057-9404 | H11 | 1 | Molex | 70543-0003 | Volume Production | Avnet | 0705430003 | 0.42149 | 0.42149
 | 652-MH2029-300Y | 652-MH2029-300Y | L1 | 1 | Bourns | MH2029-300Y | Volume Production | DigiKey | MH2029-300YCT-ND | 0.1 | 0.1
 | SMD Inductor |  | L2 | 1 | Pulse Electronics | BSCY00160808100MCP | Volume Production | DigiKey | 553-BSCY00160808100MCPCT-ND | 0.1 | 0.1
 | [Res] SMD Resistor | Generic | R1, R2 | 2 | Vishay | MCT06030C2709FP500 | Volume Production | DigiKey | 749-1631-1-ND | 0.1 | 0.2
 | [Res] SMD Resistor | Generic | R3, R8, R10, R12, R13, R14, R15, R16 | 8 | Stackpole Electronics | RMCF0603FT1K00 | Volume Production | DigiKey | RMCF0603FT1K00DKR-ND | 0.007 | 0.07
 | [Res] SMD Resistor | Generic | R4, R5 | 2 | Yageo Group | RC0603FR-075K1L | Volume Production | DigiKey | 311-5.10KHRDKR-ND | 0.007 | 0.07
 | [Res] SMD Resistor | Generic | R6 | 1 | Susumu | RR0816Q-330-D | Not Recommended for New Design | DigiKey | RR08Q33DCT-ND | 0.1 | 0.1
 | [Res] SMD Resistor | Generic | R7, R9, R11, R17 | 4 | Panasonic | ERA3ARB202V | Volume Production | DigiKey | P2.0KBDCT-ND | 0.35 | 1.4
 | Standard pushbutton |  | S1, S2 | 2 | TE Connectivity | 1825910-6 | Volume Production | DigiKey | 450-1650-ND | 0.13 | 0.26
 | W25Q128JVS | W25Q128JVSIQ TR | U1 | 1 | Winbond | W25Q128JVSIQ TR | Unknown | DigiKey | 256-W25Q128JVSIQTRCT-ND | 2.13 | 2.13
 | RP2350B | QFN-80 Package | U2 | 1 | Raspberry Pi | SC1510-A4 | Unknown | DigiKey | 2648-SC1510-A4CT-ND | 1 | 1
 | [IC] Level Shifter (2) | TXS0108EQPWRQ1 | U3 | 1 | Texas Instruments | TXS0108EQPWRQ1 | Volume Production | DigiKey | 296-42401-1-ND | 2.05 | 2.05
 | USB-C |  | X1 | 1 | JAE Electronics | DX07S024JA1R1300 | Volume Production | DigiKey | 670-3104-1-ND | 2.1 | 2.1
 | 12MHz | 815-ABM8-272-T3 | Y1 | 1 | Abracon | ABM8-272-T3 | Volume Production | DigiKey | 535-ABM8-272-T3CT-ND | 0.66 | 0.66

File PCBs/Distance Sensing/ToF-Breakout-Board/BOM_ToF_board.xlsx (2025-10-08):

Country of Origin may be different at time of shipment.
The HTSUS and ECCN information shown is for informational purposes only and is not a representation or warranty as to the accuracy or reliability of these classifications. All information is provided "as is" and is subject to change without notice. Any use made of the information provided is without recourse to Digi-Key and at the user's risk.
Index | Designator | Manufacturer Part Number | Manufacturer Name | Description | Lead Time | Availability | Stock Status | Attrition % | Requested Quantity 1 | Pack Quantity 1 | Pack Type 1 | Digi-Key Part Number 1 | Unit Price 1 | Extended Price 1 | Minimum Order Quantity 1 | Customer Reference | Requested Part Number | Lead Weeks | Datasheet | Reference Designator | US Import Tariff | Note | Part Status | RoHS Status | Moisture Sensitivity Level (MSL) | ECCN | HTSUS | Country of Origin | Environmental Information | Original Part numbers | Image | Product Notes
1 | D1 | 150060YS75000 | Würth Elektronik | LED YELLOW CLEAR 0603 SMD |  | 85,434 | In Stock |  | 7 | 7 | Cut Tape (CT) | 732-4981-1-ND | 0.15000 | $1.05 | 1 |  | 732-4981-2-ND | 11 | https://www.we-online.com/components/products/datasheet/150060YS75000.pdf |  | May apply on shipments to the U.S. |  | Active | ROHS3 Compliant | 3 (168 Hours) | EAR99 | 8541.41.0000 | China | https://mm.digikey.com/Volume0/opasdata/d220001/medias/docus/744/Certificate_of_Compliance_ROHS.pdf | 732-4981-2-ND | https://mm.digikey.com/Volume0/opasdata/d220001/medias/images/2958/WL-SMCW%20Series%200603.jpg
2 | R1 | RC0603FR-07220RL | YAGEO | RES 220 OHM 1% 1/10W 0603 |  | 313,724 | In Stock |  | 10 | 10 | Cut Tape (CT) | 311-220HRCT-ND | 0.00900 | $0.09 | 1 |  | 311-220HRTR-ND | 18 | https://www.yageogroup.com/content/datasheet/asset/file/PYU-RC_GROUP_51_ROHS_L |  | N/A |  | Active | ROHS3 Compliant | 1 (Unlimited) | EAR99 | 8533.21.0030 | Taiwan | https://www.yageo.com/en/Download/Index/certificates#rchip | 311-220HRTR-ND | https://mm.digikey.com/Volume0/opasdata/d220001/medias/images/4322/cut-tape-render.jpg
3 | R2 | RC0603FR-0710KL | YAGEO | RES 10K OHM 1% 1/10W 0603 |  | 15,705,619 | In Stock |  | 10 | 10 | Cut Tape (CT) | 311-10.0KHRCT-ND | 0.00900 | $0.09 | 1 |  | 311-10.0KHRCT-ND | 18 | https://www.yageogroup.com/content/datasheet/asset/file/PYU-RC_GROUP_51_ROHS_L |  | N/A |  | Active | ROHS3 Compliant | 1 (Unlimited) | EAR99 | 8533.21.0030 | Taiwan | https://www.yageo.com/en/Download/Index/certificates#rchip | 311-10.0KHRCT-ND | https://mm.digikey.com/Volume0/opasdata/d220001/medias/images/4322/cut-tape-render.jpg
4 | C1, C2 | C0603C104K5RACTU | KEMET | CAP CER 0.1UF 50V X7R 0603 |  | 7,063,446 | In Stock |  | 20 | 20 | Cut Tape (CT) | 399-C0603C104K5RACTUCT-ND | 0.01100 | $0.22 | 1 |  | 399-C0603C104K5RACTUCT-ND | 15 | https://search.kemet.com/download/datasheet/C0603C104K5RAC7867 |  | May apply on shipments to the U.S. |  | Active | ROHS3 Compliant | 1 (Unlimited) | EAR99 | 8532.24.0020 | China |  | 399-C0603C104K5RACTUCT-ND | https://mm.digikey.com/Volume0/opasdata/d220001/medias/images/4322/cut-tape-render.jpg
5 | C3 | GRM188R61E475KE11D | Murata Electronics | CAP CER 4.7UF 25V X5R 0603 |  | 562,884 | In Stock |  | 10 | 10 | Cut Tape (CT) | 490-7203-1-ND | 0.03600 | $0.36 | 1 |  | 490-7203-1-ND | 12 | https://search.murata.co.jp/Ceramy/image/img/A01X/G101/ENG/GRM188R61E475KE11-01.pdf |  | N/A |  | Active | ROHS3 Compliant | 1 (Unlimited) | EAR99 | 8532.24.0020 | Japan |  | 490-7203-1-ND | https://mm.digikey.com/Volume0/opasdata/d220001/medias/images/4322/cut-tape-render.jpg
6 | U1 | VL53L1CXV0FY/1 | STMicroelectronics | SENSOR OPTICAL 0-62CM I2C |  | 13,004 | In Stock |  | 7 | 7 | Cut Tape (CT) | 497-17764-1-ND | 5.18400 | $36.29 | 1 |  | 497-17764-1-ND | 16 | https://www.st.com/resource/en/datasheet/vl53l1x.pdf |  | May apply on shipments to the U.S. |  | Active | ROHS3 Compliant | 3 (168 Hours) | EAR99 | 9031.80.8085 | China |  | 497-17764-1-ND | https://mm.digikey.com/Volume0/opasdata/d220001/medias/images/2878/MFG_VL53L1CXV0FY%5E1.jpg

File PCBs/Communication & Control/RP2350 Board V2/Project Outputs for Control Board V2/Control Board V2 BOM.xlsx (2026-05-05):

 | Bill of Materials
Project Name: | Control Board V2.PrjPcb
Part Number | Designator | Manufacture | Manufacture Part Number | Supplier | Supplier Part Number | Supplier Unit Price | Quantity
[LED] SMD 0805 Green | D1 | Osram Opto | LG R971-KN-1-0-20-R18 | DigiKey | 475-LGR971-KN-1CT-ND | $0.15 | 1
[LED] SMD 0805 Yellow | D2 | Osram | LY R976-PS-36-0-20-R18 | DigiKey | 475-LYR976-PS-36-0-20-R18CT-ND | $0.15 | 1
[LED] SMD 0805 Red | D3 | Osram Opto | LS R976-NR-1-0-20-R18 | DigiKey | 475-LSR976-NR-1CT-ND | $0.15 | 1
[LED] SMD 0805 Blue | D4, D5 | Wurth Elektronik | 150080BS75000 | DigiKey | 732-4982-1-ND | $0.19 | 2
[Header] Shrouded 2x5 Male | H1, H2, H3 | Adam Tech | BHR-10-VUA | DigiKey | 2057-BHR-10-VUA-ND | $0.28 | 3
[Header] Shrouded 1x3 Male | H4, H5, H6, H7, H8, H9, H10, H12, H13, H14 | Molex | 70543-0037 | DigiKey | WM4825-ND | $0.78 | 10
[Header] Shrouded 1x2 Male | H11 | Molex | 70543-0036 | DigiKey | WM4824-ND | $0.92 | 1
[Header] Shrouded 1x6 Male | H15 | Molex | 70543-0005 | DigiKey | WM4804-ND | $1.15 | 1
[Ferrite] SMD 0805 3A 30ohm | L1 | Bourns | MH2029-300Y | DigiKey | MH2029-300YCT-ND | $0.10 | 1
[220] SMD 0603 1% 1/10W | R1, R2, R3 | TE Connectivity | CRGCQ0805F220R | DigiKey | A129741CT-ND | $0.14 | 3
[1k] SMD 0603 1% 1/10W | R4, R5 | Stackpole Electronics | RMCF0603FT1K00 | DigiKey | RMCF0603FT1K00DKR-ND | $0.01 | 2
[Level Shifter] MC14504BDTR2G Breakout | X1 | onsemi | MC14504BDTR2G | DigiKey | MC14504BDTR2GOSCT-ND | $0.66 | 1
[Pi] RP2350B Breakout | X2 |  |  |  |  |  | 1
[Screw Terminal] 3pin | X4 | Same Sky | TB003-500-P03BE | DigiKey | 102-6162-ND | $0.62 | 1
 |  |  |  |  |  | $5.30 | 29
Notes

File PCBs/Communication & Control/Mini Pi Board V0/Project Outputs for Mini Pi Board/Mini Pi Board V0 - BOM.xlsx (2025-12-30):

Line # | Name | Description | Designator | Quantity | Manufacturer 1 | Manufacturer Part Number 1 | Manufacturer Lifecycle 1 | Supplier 1 | Supplier Part Number 1 | Supplier Unit Price 1 | Supplier Subtotal 1
 | SMD LED | Generic | D1 | 1 | Osram Opto | LG R971-KN-1-0-20-R18 | Unknown | DigiKey | 475-LGR971-KN-1CT-ND | 0.15 | 0.15
 | SMD LED | Generic | D2 | 1 | Osram | LY R976-PS-36-0-20-R18 | Unknown | DigiKey | 475-LYR976-PS-36-0-20-R18CT-ND | 0.15 | 0.15
 | SMD LED | Generic | D3 | 1 | Osram Opto | LS R976-NR-1-0-20-R18 | Unknown | DigiKey | 475-LSR976-NR-1CT-ND | 0.15 | 0.15
 | 1x3 Male | 070543-0037 Mates with 005057-9403 | H1 | 1 | Molex | 50-57-9403 | Volume Production | DigiKey | WM2901-ND | 0.22 | 0.22
 | 652-MH2029-300Y | 652-MH2029-300Y | L1 | 1 | Bourns | MH2029-300Y | Volume Production | DigiKey | MH2029-300YCT-ND | 0.1 | 0.1
 | [Res] SMD Resistor | Generic | R1, R2, R3 | 3 | Stackpole Electronics | RMCF0603FT1K00 | Volume Production | DigiKey | RMCF0603FT1K00DKR-ND | 0.007 | 0.07
 | Raspberry Pi 5 | Raspberry Pi 5 | X1 | 1 | Omron | XG4H-4034 | Volume Production | DigiKey | XG4H-4034-ND | 5.16 | 5.16
 | 4pin Screw Terminal |  | X2 | 1 | Same Sky | TB002-500-04BE | Volume Production | DigiKey | 102-6147-ND | 0.77 | 0.77

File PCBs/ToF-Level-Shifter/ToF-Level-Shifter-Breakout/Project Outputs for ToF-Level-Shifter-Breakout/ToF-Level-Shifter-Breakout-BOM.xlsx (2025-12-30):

Comment | Description | Designator | Footprint | LibRef | Quantity | DigiKey link
Cap | 4.7uF 0603 ceramic cap | C4 | CAPC0603 | Cap | 1 | https://www.digikey.com/en/products/detail/samsung-electro-mechanics/CL10A475KO8NNNC/3887442
Cap | 0.1uF 0603 ceramic cap | C1, C2, C3 | CAPC0603 | Cap | 3 | https://www.digikey.com/en/products/detail/samsung-electro-mechanics/CL10F104ZB8NNNC/3886670
1x4 0.1in Header |  | P1 | 1x4 0.1in Header | 1x4 0.1in Header | 0 | Just use a standard 2.54mm pitch header
Header 7 | Header, 7-Pin | P2 | HDR1X7 | Header 7 | 0 | ^
Res | 300kohm RES 0603 | R2 | RES0603 | Res | 1 | https://www.digikey.com/en/products/detail/rohm-semiconductor/ESR03EZPJ304/4051237
Res | 200kohm RES 0603 | R1 | RES0603 | Res | 1 | https://www.digikey.com/en/products/detail/rohm-semiconductor/ESR03EZPJ204/4051216
Res | 10kohm RES0603 | R3, R4, R5, R6, R7 | RES0603 | Res | 5 | https://www.digikey.com/en/products/detail/rohm-semiconductor/ESR03EZPF1002/1983429
ADPL40502AUJZ-1.8-R7 | Low Noise, 200mA, CMOS Linear Regulator (LDO) | U1 | TSOT-23-5_UJ-5_ADI | ADPL40502AUJZ-1.8-R7 | 1 | https://www.digikey.com/en/products/detail/analog-devices-inc/ADPL40502AUJZ-1-8-R7/26262777
PCA9306DCTR | 2-bit bidirectional 400-kHz I2C/SMBus voltage level translator | U2 | SOP65P400X130-8N | PCA9306DCTR | 1 | https://www.digikey.com/en/products/detail/texas-instruments/PCA9306DCTR/809792
VL53L1CXV0FY/1 | ToF Optical Sensor 157.480 (4m) I²C Output from STMelectronics | U3 | LGA-12 (VL53L1CXV0FY/1) | VL53L1CXV0FY/1 | 0 | Use ones that have already been ordered
DigiKey Link: https://www.digikey.com/en/mylists/list/5HL9NZVCED |  |  |  |  | 13
Collaborator PW: MIL2025!

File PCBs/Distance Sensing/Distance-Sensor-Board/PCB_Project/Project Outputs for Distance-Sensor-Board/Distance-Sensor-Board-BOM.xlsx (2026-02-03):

Added to List? | Comment | Description | Designator | Footprint | LibRef | Quantity | DigiKey Link | Notes
TRUE | BOOT | SWITCH TACTILE SPST-NO 0.05A 24V | B1, B2 | SPST-PUSH-BUTTON | 1825910-6 | 2 | https://www.digikey.com/en/products/detail/te-connectivity-alcoswitch-switches/1825910-6/1632536
TRUE | 10uF | 10uF electrolytic cap, radial can, SMD | C1, C2 | RADIAL_CAN_CAP_4_X_5.8_SMD | EEE-FK1E100R | 2 | https://www.digikey.com/en/products/detail/panasonic-electronic-components/EEE-FK1E100R/765964
TRUE | Cap | 4.7uF ceramic cap | C4, C5, C6, C10 | CAP0603 | Cap | 4 | https://www.digikey.com/en/products/detail/samsung-electro-mechanics/CL10A475KO8NNNC/3887442
TRUE | Cap | 100pF ceramic cap | C38 | CAP0603 | Cap | 1 | https://www.digikey.com/en/products/detail/murata-electronics/GRM0335C1E101JA01D/702426
TRUE | Cap | 1uF ceramic cap | C25, C26 | CAP0603 | Cap | 2 | https://www.digikey.com/en/products/detail/samsung-electro-mechanics/CL10B105MO8NNWC/5961008
TRUE | Cap | 100nF ceramic cap | C3, C7, C8, C9, C11, C12, C13, C14, C15, C16, C17, C18, C19, C20, C21, C22, C23, C24, C27, C28, C29, C30, C31, C32, C33, C34, C35, C36, C37 | CAPC0603 | Cap | 29 | https://www.digikey.com/en/products/detail/samsung-electro-mechanics/CL10F104ZB8NNNC/3886670
TRUE | MF-MSMF050-2 | [Fuse] Polymeric PTC Resettable Fuse 15V 500 mA Ih Surface Mount 1812 (4532 Metric), Concave | F1 | FUSM4632X85 | MF-MSMF050-2 | 1 | https://www.digikey.com/en/products/detail/bourns-inc/MF-MSMF050-2/662816
TRUE | MH2029-300Y | [Inductor] FB 0805 | FB1 | L0805 | MH2029-300Y | 1 | https://www.digikey.com/en/products/detail/bourns-inc/MH2029-300Y/2563323
TRUE | USB-B | USB-B (USB TYPE-B) USB 2.0 Receptacle Connector 4 Position Through Hole, Right Angle | J1 | SAMTEC_USB-B-S-X-X-TH | USB-B-S-X-X-TH | 1 | https://www.digikey.com/en/products/detail/samtec-inc/USB-B-S-F-B-TH/2686101
FALSE | Thru-Hole Jumper | Clip Jumper | J2, J4 | [Jumper] Solderable Jumper | [Jump] Thru-Hole 2pin | 2 |  | Just pads on PCB
TRUE | [Connector] 879142016 | 2x10 2.54mm pitch header | J3 | [Connector] CONN20 | [Connector] 879142016 | 1 | Just pads and standard header
TRUE | 3.3uH | Power Inductors - SMD IND 3.3uH used for RP2350 VREG | L1 | 2016_SMD_Inductor | INDUCTOR 3.3uH | 1 | https://www.digikey.com/en/products/detail/abracon-llc/AOTA-B201610S3R3-101-T/25621527
TRUE | 2 port screw | 2 Position Wire to Board Terminal Block Horizontal with Board 0.200 (5.08mm) Through Hole | P1 | [CONNECTOR] 5MM_2PORT_SCREW | [Connector] 691213510002 | 1 | https://www.digikey.com/en/products/detail/w%C3%BCrth-elektronik/691213510002/11477374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
TRUE | UART | Header, Molex, 2mm Pitch Sherlock Header, Single Row, Right Angle 3 Circuits, Length 3.3mm | P2 | MOLEX-HDR-1X3-SHERLOCK-RA | MOLEX-HDR-1x3-SHERLOCK_RA | 1 | https://www.digikey.com/en/products/detail/molex/0353630360/755311?gclsrc=aw.ds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
TRUE | FDN340P | [MOSFET-P] P-Channel 20 V 2A (Ta) 500mW (Ta) Surface Mount SOT-23-3 | Q1 | SOT95P240X120-3N | [PMOS] FDN340P | 1 | https://www.digikey.com/en/products/detail/onsemi/FDN340P/965304
TRUE | Res | 33 ohm res | R1 | RES0603 | Res | 1 | https://www.digikey.com/en/products/detail/bourns-inc/MH2029-300Y/2563323
TRUE | Res | 27 ohm res | R2, R3 | RES0603 | Res | 2 | https://www.digikey.com/en/products/detail/te-connectivity-passive-product/CRGP0603F27R/8576999
TRUE | Res | 1k ohm res | R4, R5, R6 | RES0603 | Res | 3 | https://www.digikey.com/en/products/detail/stackpole-electronics-inc/RMCP0603FT1K00/6269097
TRUE | Res | 300k ohm res | R10 | RES0603 | Res | 1 | https://www.digikey.com/en/products/detail/rohm-semiconductor/ESR03EZPJ304/4051237
TRUE | Res | 200k ohm res | R7 | RES0603 | Res | 1 | https://www.digikey.com/en/products/detail/rohm-semiconductor/ESR03EZPJ204/4051216
TRUE | Res | 10k ohm res | R8, R9, R11, R12 | RES0603 | Res | 4 | https://www.digikey.com/en/products/detail/rohm-semiconductor/ESR03EZPF1002/1983429
TRUE | ToF 1 | 1x7 2mm pitch sherlock connector | ToF1 | 7POS_2MM_CONN | MOLEX_SHERLOCK_1x7_CONN | 1 | https://www.digikey.com/en/products/detail/molex/0353620750/773856
TRUE | ToF 2 | 1x7 2mm pitch sherlock connector | ToF2 | 7POS_2MM_CONN | MOLEX_SHERLOCK_1x7_CONN | 1 | ^ | corresponding female receptacles also in list
TRUE | ToF 3 | 1x7 2mm pitch sherlock connector | ToF3 | 7POS_2MM_CONN | MOLEX_SHERLOCK_1x7_CONN | 1 | ^
TRUE | ToF 4 | 1x7 2mm pitch sherlock connector | ToF4 | 7POS_2MM_CONN | MOLEX_SHERLOCK_1x7_CONN | 1 | ^
TRUE | [MCU] RP2350 | RP2350A MCU from Raspberry Pi Pico; QFN 60 7x7, | U1 | QFN40P700X700X90-61N | SC1509(13) | 1 | https://www.digikey.com/en/products/detail/raspberry-pi/SC1509-13/26241107
TRUE | NCP1117LPST33T3G | Linear Voltage Regulator IC Positive Fixed 1 Output 1A SOT-223 | U2 | SOT230P700X175-4N | NCP1117LPST33T3G | 1 | https://www.digikey.com/en/products/detail/onsemi/NCP1117LPST33T3G/2194024
TRUE | LMV358IDR | [Op-Amp] Dual, 5.5-V, 1-MHz, RRO operational amplifier 8-SOIC -40 to 125 | U3 | SOIC-8 | LMV358IDR | 1 | https://www.digikey.com/en/products/detail/texas-instruments/LMV358IDR/381251
TRUE | W25Q128JVSIQ TR | IC FLASH 128MBIT SPI/QUAD 8SOIC | U4 | SOIC_208MIL_WIN | W25Q128JVSIQ TR | 1 | https://www.digikey.com/en/products/detail/winbond-electronics/W25Q128JVSIQ-TR/5803944
TRUE | ADPL40502AUJZ-1.8-R7 | Low Noise, 200mA, CMOS Linear Regulator (LDO) | U5 | TSOT-23-5_UJ-5_ADI | ADPL40502AUJZ-1.8-R7 | 1 | https://www.digikey.com/en/products/detail/analog-devices-inc/ADPL40502AUJZ-1-8-R7/26262777
TRUE | PCA9306DCTR | 2-bit bidirectional 400-kHz I2C/SMBus voltage level translator | U6 | SOP65P400X130-8N | PCA9306DCTR | 1 | https://www.digikey.com/en/products/detail/texas-instruments/PCA9306DCTR/809792
TRUE | USS1 | Header, Molex, 2mm Pitch Sherlock Header, Single Row, Vertical, 4 Circuits, Length 3.3mm, 0353620450 | US1 | MOLEX-HDR-1X4-SHERLOCK-VERT | MOLEX-HDR-1x4-SHERLOCK_VERT | 1 | https://www.digikey.com/en/products/detail/molex/0353620450/773855
TRUE | USS2 | Header, Molex, 2mm Pitch Sherlock Header, Single Row, Vertical, 4 Circuits, Length 3.3mm, 0353620450 | US2 | MOLEX-HDR-1X4-SHERLOCK-VERT | MOLEX-HDR-1x4-SHERLOCK_VERT | 1 | ^ | corresponding female receptacles in digikey list
TRUE | USS3 | Header, Molex, 2mm Pitch Sherlock Header, Single Row, Vertical, 4 Circuits, Length 3.3mm, 0353620450 | US3 | MOLEX-HDR-1X4-SHERLOCK-VERT | MOLEX-HDR-1x4-SHERLOCK_VERT | 1 | ^
TRUE | USS4 | Header, Molex, 2mm Pitch Sherlock Header, Single Row, Vertical, 4 Circuits, Length 3.3mm, 0353620450 | US4 | MOLEX-HDR-1X4-SHERLOCK-VERT | MOLEX-HDR-1x4-SHERLOCK_VERT | 1 | ^
TRUE | ABM8-272-T3 | 12 MHz Â±30ppm Crystal 10pF 50 Ohms 4-SMD, No Lead | Y1 | XTAL_ABM8-272-T3 | ABM8-272-T3 | 1 | https://www.digikey.com/en/products/detail/abracon-llc/ABM8-272-T3/22472366
TRUE | VAR | [Varistor] 1 Circuit Surface Mount, MLCV 0603 (1608 Metric) | Z1, Z2 | VARC1608X56N | CG0603MLC-05E | 2 | https://www.digikey.com/en/products/detail/bourns-inc/CG0603MLC-05E/2538084
DigiKey List: https://www.digikey.com/en/mylists/list/SDWFYLVJXC |  |  |  |  |  | 79
Collaborator PW: MIL2025!

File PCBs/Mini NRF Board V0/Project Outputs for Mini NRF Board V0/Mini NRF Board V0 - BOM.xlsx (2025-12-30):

Line # | Name | Description | Designator | Quantity | Manufacturer 1 | Manufacturer Part Number 1 | Manufacturer Lifecycle 1 | Supplier 1 | Supplier Part Number 1 | Supplier Unit Price 1 | Supplier Subtotal 1
 | RP-SMA 50-Ohm | PCB.RPSMAFRA.HT | A1 | 1 | Taoglas | PCB.RPSMAFRA.HT | Unknown | DigiKey | 931-1360-ND | 3.59 | 3.59
 | SMD Nonpolarized |  | C1, C2 | 2 | Cal-Chip Electronics | CHV0603N2501R2BCT | Unknown | DigiKey | 4713-CHV0603N2501R2BCT-ND | 0.22 | 0.44
 | SMD Nonpolarized |  | C3 | 1 | Johanson | QSCP251Q0R3A1GV001T | Volume Production | DigiKey | 712-QSCP251Q0R3A1GV001TCT-ND | 0.44 | 0.44
 | SMD Nonpolarized |  | C4 | 1 | Yageo Group | CC0603JRX7R7BB105 | Volume Production | DigiKey | 311-3485-1-ND | 0.2 | 0.2
 | SMD Nonpolarized |  | C5 | 1 | KEMET | C0603C221J5GAC7411 | Volume Production | DigiKey | 399-C0603C221J5GAC7411CT-ND | 0.1 | 0.1
 | SMD Nonpolarized |  | C6 | 1 | Yageo Group | CC0603CRNPO9BN1R0 | Volume Production | DigiKey | 311-1049-1-ND | 0.1 | 0.1
 | SMD Nonpolarized |  | C7 | 1 | Yageo Group | CC0603BRNPO9BN1R5 | Volume Production | DigiKey | 311-1737-1-ND | 0.1 | 0.1
 | SMD Nonpolarized |  | C8 | 1 | Yageo Group | CC0603CPNPO9BN4R7 | Volume Production | DigiKey | 13-CC0603CPNPO9BN4R7CT-ND | 0.1 | 0.1
 | SMD Nonpolarized |  | C9 | 1 | Murata | GRM1885C1H222JA01D | Volume Production | DigiKey | 490-1459-1-ND | 0.1 | 0.1
 | SMD Nonpolarized |  | C10, C13 | 2 | Yageo Group | CC0603FRNPO9BN150 | Volume Production | DigiKey | 311-3887-1-ND | 0.14 | 0.28
 | SMD Nonpolarized |  | C11 | 1 | Murata | GRM1885C1H102JA01D | Volume Production | DigiKey | 490-1451-6-ND | 0.08 | 0.08
 | SMD Nonpolarized |  | C12 | 1 | Yageo Group | CC0603JRX7R9BB333 | Volume Production | DigiKey | 311-4015-1-ND | 0.1 | 0.1
 | SMD Nonpolarized |  | C14 | 1 | KEMET | C0603C103J5RACTU | Volume Production | DigiKey | 399-C0603C103J5RACTUDKR-ND | 0.08 | 0.08
 | 1x2 Male | 0705430036 Mates with 0050579402 | H1 | 1 | Molex | 50-57-9402 | Volume Production | DigiKey | WM2900-ND | 0.31 | 0.31
 | [Header] Shrouded 1x6 Male | 0705430005 Mates with 0050579406 | H2 | 1 | Molex | 50-57-9406 | Volume Production | DigiKey | WM2904-ND | 0.4 | 0.4
 | SMD Inductor |  | L1 | 1 | Wurth Elektronik | 7447860027G | Unknown | DigiKey | 732-7447860027GCT-ND | 0.1 | 0.1
 | SMD Inductor |  | L2 | 1 | Murata | LQG18HN3N9S00D | Volume Production | DigiKey | 490-1105-1-ND | 0.14 | 0.14
 | SMD Inductor |  | L3 | 1 | Murata | LQG18HN8N2J00D | Volume Production | DigiKey | 490-1109-1-ND | 0.14 | 0.14
 | SMD Inductor |  | L4 | 1 | Murata | LQG18HN2N7S00D | Volume Production | DigiKey | 490-1103-1-ND | 0.14 | 0.14
 | 652-MH2029-300Y | 652-MH2029-300Y | L5, L6 | 2 | Bourns | MH2029-300Y | Volume Production | DigiKey | MH2029-300YCT-ND | 0.1 | 0.2
 | [Res] SMD Resistor | Generic | R1, R2 | 2 | Yageo Group | RC0603FR-0710KL | Volume Production | DigiKey | 311-10.0KHRDKR-ND | 0.006 | 0.06
 | [Res] SMD Resistor | Generic | R3 | 1 | Yageo Group | RC0603FR-0722RL | Volume Production | DigiKey | 311-22.0HRDKR-ND | 0.1 | 0.1
 | [Res] SMD Resistor | Generic | R4 | 1 | Yageo Group | RT0603BRD071ML | Volume Production | DigiKey | YAG4498CT-ND | 0.1 | 0.1
 | RFX2401C | RFX2401C | U1 | 1 | Skyworks Solutions | RFX2401C | Volume Production | DigiKey | 863-1828-1-ND | 1.22 | 1.22
 | NRF24L01P | NRF24L01P-R | U2 | 1 | Nordic Semiconductor | NRF24L01P-R | Unknown | DigiKey | 4823-NRF24L01P-RCT-ND | 2.02 | 2016
 | 16 MHz | ABM11-16.000MHZ-12-N1G-T | Y1 | 1 | Abracon | ABM11-16.000MHZ-12-N1G-T | Volume Production | DigiKey | 535-14950-1-ND | 0.31 | 0.31

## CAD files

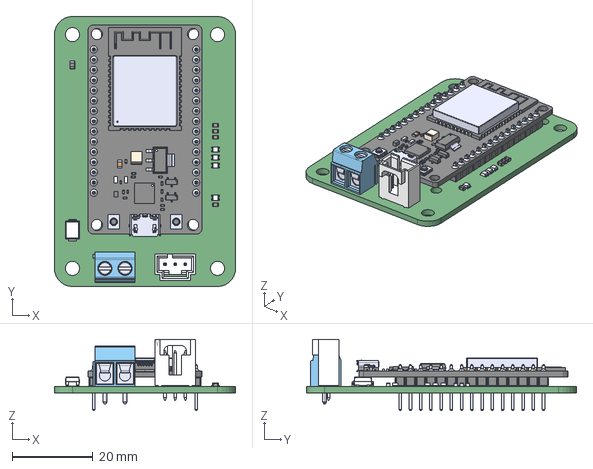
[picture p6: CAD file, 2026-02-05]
PCBs/Communication & Control/ESP32 Breakout Board V0/ESP32 Breakout Board V0 3D Model.step
45.0 x 67.0 x 17.7 mm

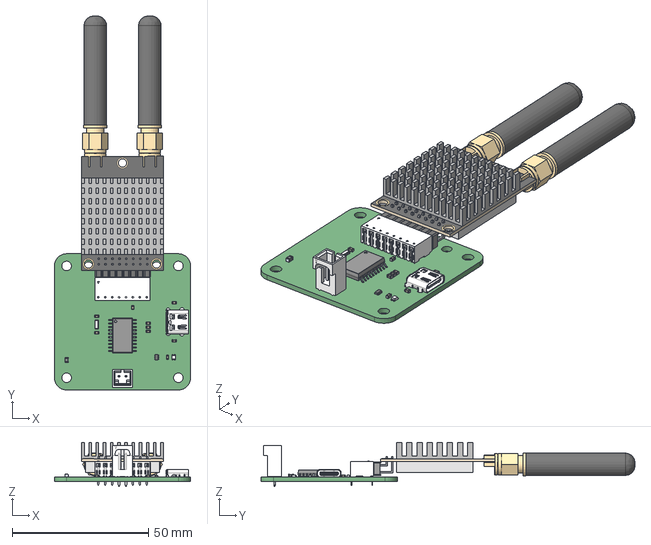
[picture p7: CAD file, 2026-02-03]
PCBs/Communication & Control/Mini RFDx900 Board V1/Mini RFDx900 Board V1 3D Model.step
50.0 x 137.2 x 16.2 mm

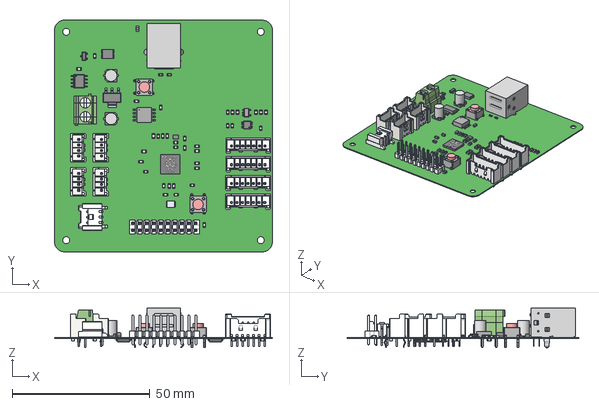
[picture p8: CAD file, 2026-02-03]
PCBs/Distance Sensing/Distance-Sensor-Board/PCB_Project/distance-sensor-board.step
79.0 x 84.0 x 14.4 mm

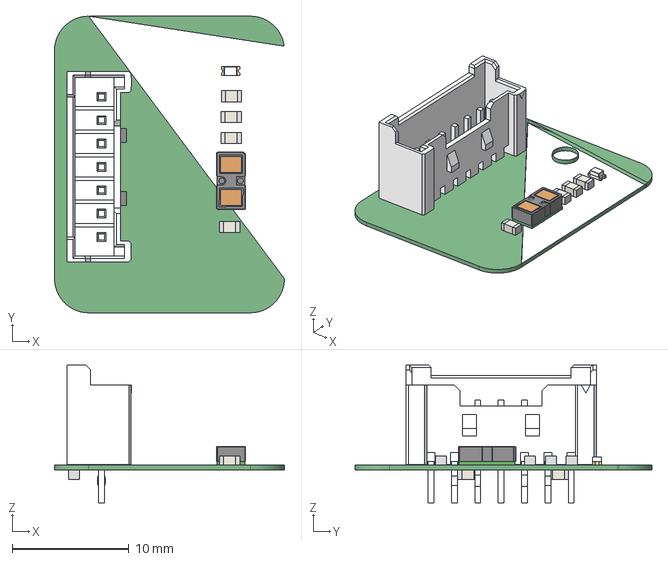
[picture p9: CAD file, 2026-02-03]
PCBs/Distance Sensing/ToF-Breakout-Board/PCB_Project/tof-breakout.step
19.7 x 25.4 x 11.8 mm

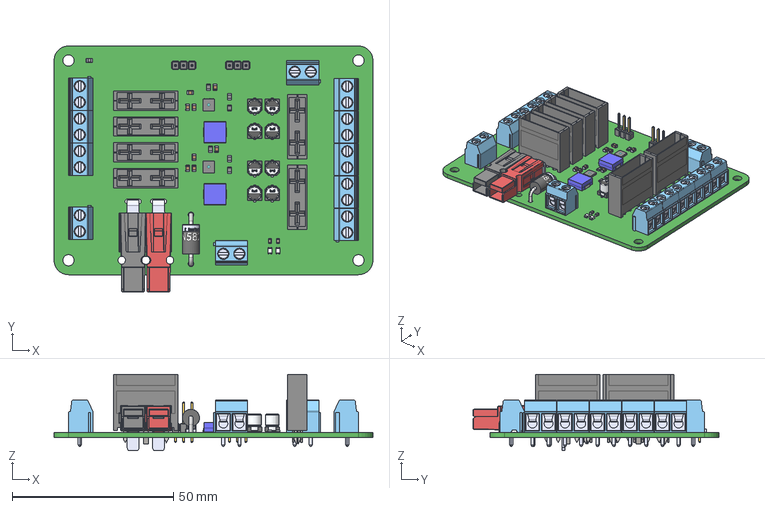
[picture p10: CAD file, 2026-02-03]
PCBs/Rover Power Board V1/Power Board V1 3D Model.step
99.0 x 76.4 x 23.7 mm

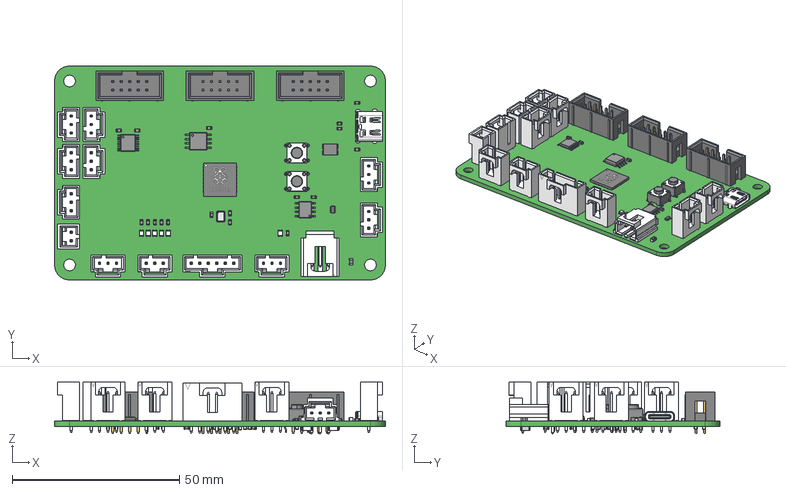
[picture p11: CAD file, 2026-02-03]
PCBs/RP2350 Board V1/RP2350 Board V1 3D Model.step
99.0 x 64.0 x 15.5 mm

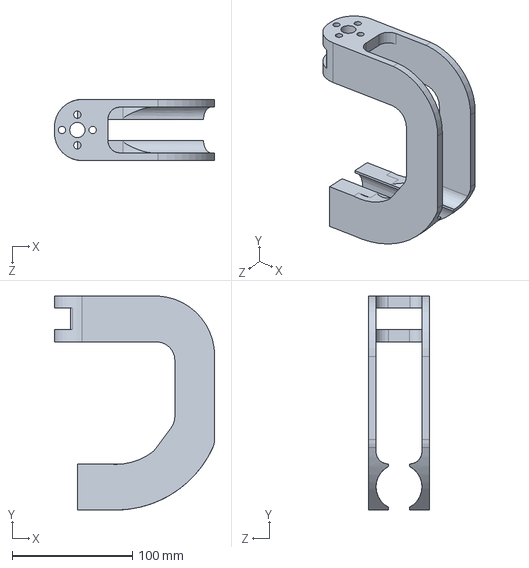
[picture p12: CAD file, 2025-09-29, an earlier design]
Deprecated or Legacy/LegacyRepo/CAD Parts/New CAD/Wheel Join Whole.SLDPRT
133.1 x 177.8 x 50.8 mm

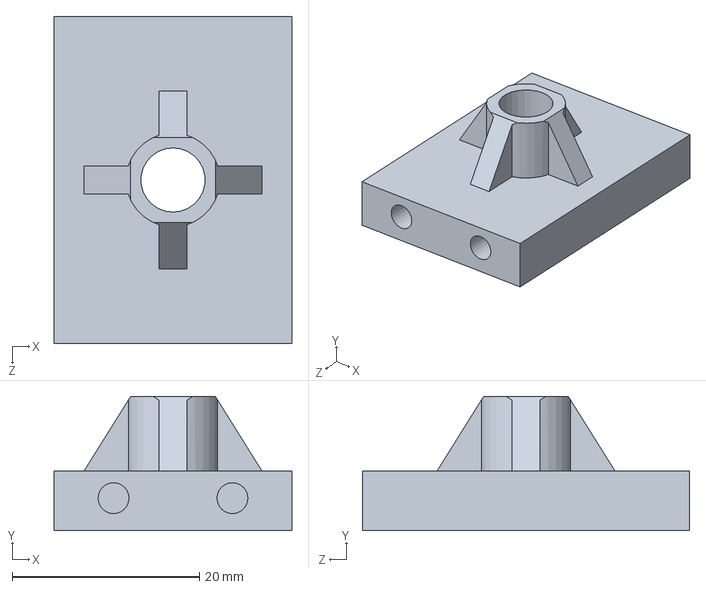
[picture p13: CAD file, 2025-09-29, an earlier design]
Deprecated or Legacy/LegacyRepo/CAD Parts/Fixed CAD/Wheel_mount.SLDPRT
25.4 x 14.3 x 34.9 mm

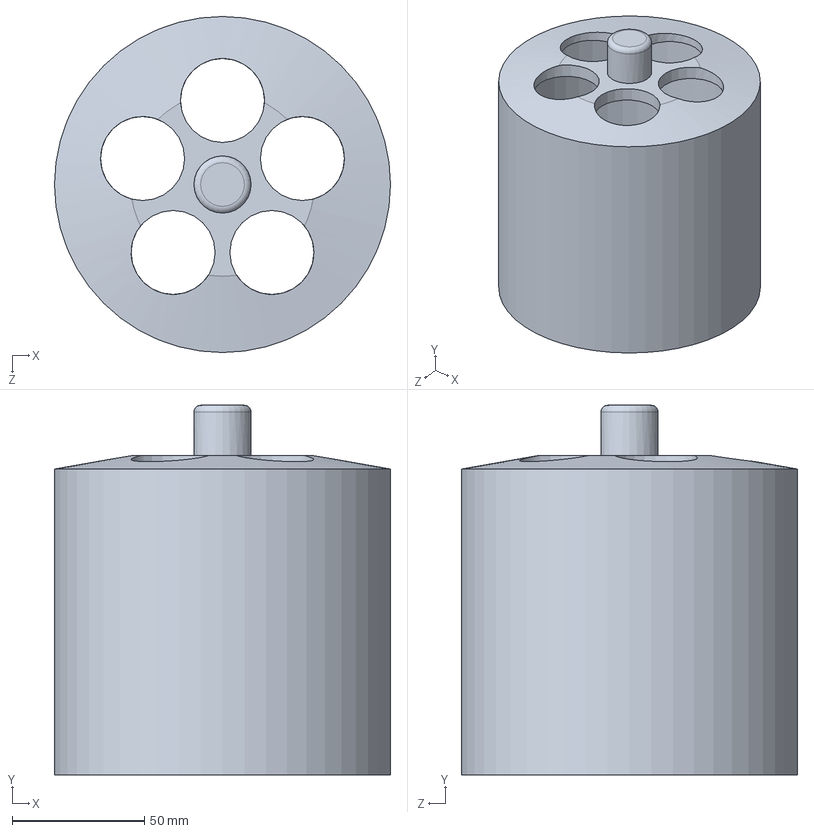
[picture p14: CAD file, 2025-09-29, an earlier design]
Deprecated or Legacy/LegacyRepo/CAD Parts/Old CAD/Wheel.SLDPRT
127.0 x 139.7 x 127.0 mm

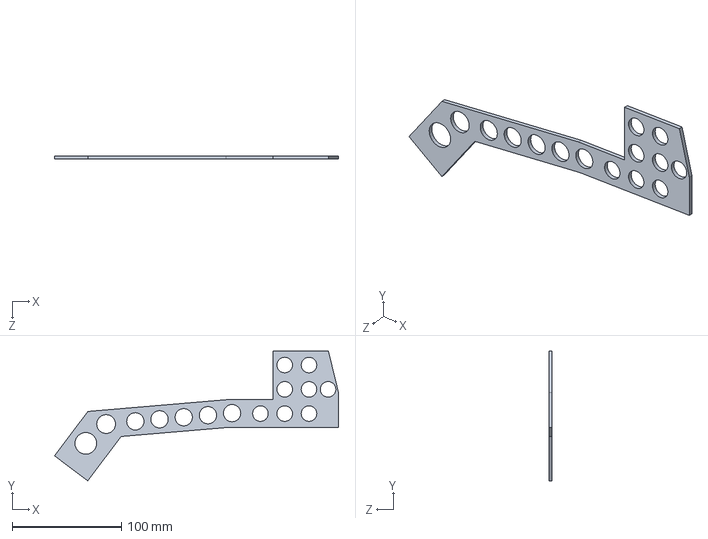
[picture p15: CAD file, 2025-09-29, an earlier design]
Deprecated or Legacy/LegacyRepo/CAD Parts/Fixed CAD/Frame_C.SLDPRT
260.0 x 118.7 x 3.17 mm

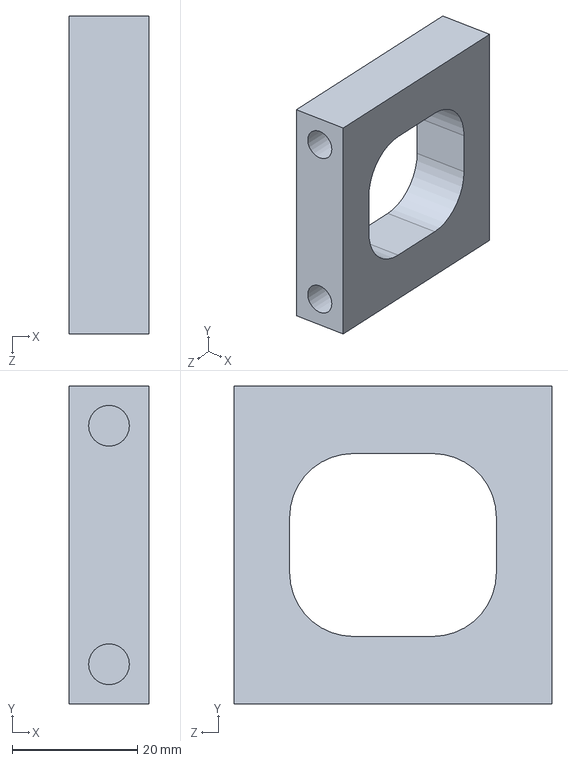
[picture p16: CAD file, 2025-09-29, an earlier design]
Deprecated or Legacy/LegacyRepo/CAD Parts/New CAD/Frame_Join_B.SLDPRT
12.7 x 50.8 x 50.8 mm

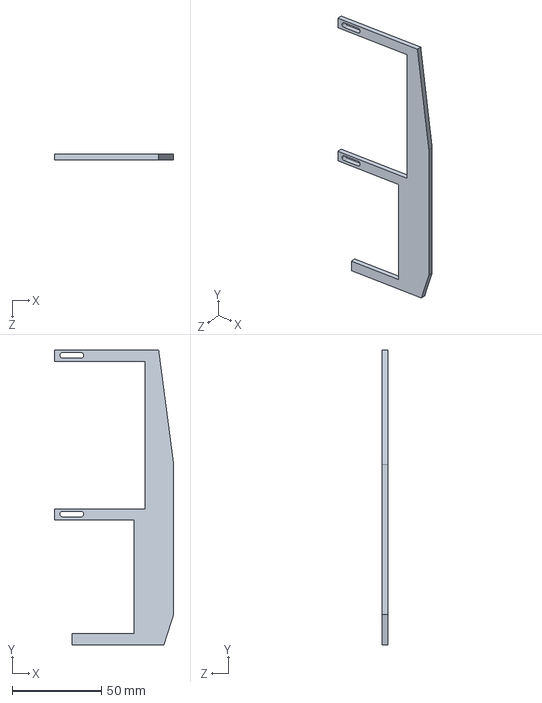
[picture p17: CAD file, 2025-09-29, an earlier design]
Deprecated or Legacy/LegacyRepo/CAD Parts/Old CAD/Wheel_Bracket.SLDPRT
66.8 x 165.1 x 3.17 mm

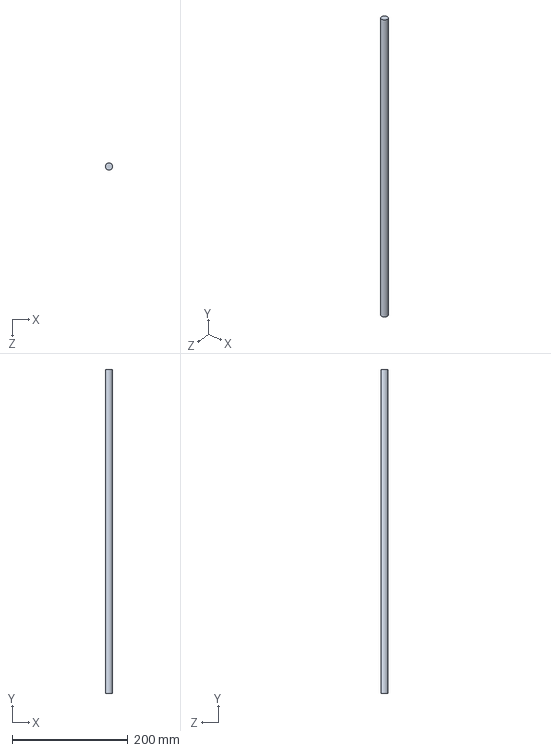
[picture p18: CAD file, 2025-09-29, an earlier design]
Deprecated or Legacy/LegacyRepo/CAD Parts/Fixed CAD/0_5_in_shaft.SLDPRT
12.7 x 558.8 x 12.7 mm

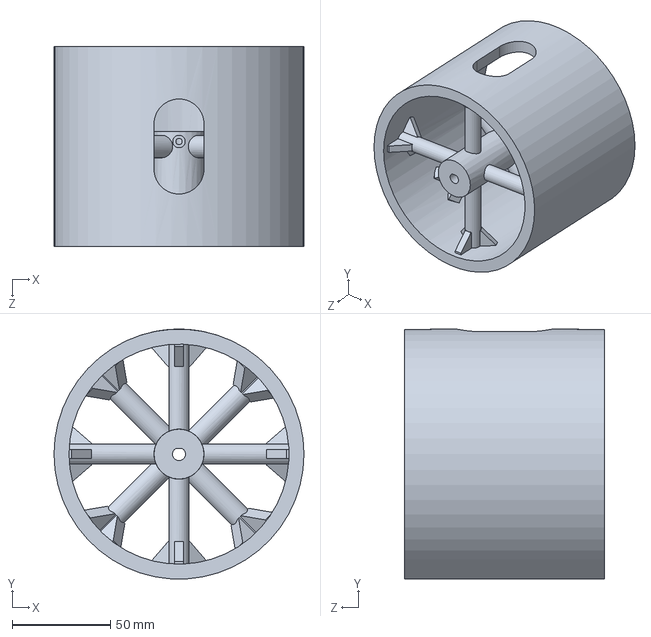
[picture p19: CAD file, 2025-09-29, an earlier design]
Deprecated or Legacy/LegacyRepo/CAD Parts/New CAD/Wheel Interior.SLDPRT
127.0 x 126.9 x 101.6 mm

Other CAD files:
PCBs/Distance Sensing/ToF-Breakout-Board/PCB_Project/ToF Sensor Breakout V1.step
Deprecated or Legacy/LegacyRepo/CAD Parts/New CAD/Wheel_Assem.SLDASM
Deprecated or Legacy/LegacyRepo/CAD Parts/Fixed CAD/0_75_in_shaft.SLDPRT
Deprecated or Legacy/LegacyRepo/CAD Parts/Fixed CAD/3_in_pin.SLDPRT
Deprecated or Legacy/LegacyRepo/CAD Parts/Fixed CAD/Chassis.SLDPRT
Deprecated or Legacy/LegacyRepo/CAD Parts/Fixed CAD/Frame_A.SLDPRT
Deprecated or Legacy/LegacyRepo/CAD Parts/Fixed CAD/Frame_B.SLDPRT
Deprecated or Legacy/LegacyRepo/CAD Parts/Fixed CAD/Swerve_mount.SLDPRT
Deprecated or Legacy/LegacyRepo/CAD Parts/New CAD/DC Motor.SLDPRT
Deprecated or Legacy/LegacyRepo/CAD Parts/New CAD/Frame_Join_A.SLDPRT
Deprecated or Legacy/LegacyRepo/CAD Parts/New CAD/Motor Mount.SLDPRT
Deprecated or Legacy/LegacyRepo/CAD Parts/New CAD/Shaft Coupler.SLDPRT
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

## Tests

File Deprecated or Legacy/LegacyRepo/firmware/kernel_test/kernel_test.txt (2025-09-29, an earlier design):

HELLO WORLD
Time between interrupts: 0
Interrupt was triggered and ISR was called Time between two: 1000

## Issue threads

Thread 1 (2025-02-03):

Battery Monitor Board

MjAdrian, 2025-02-03:
**Deadline: 04/01/2025**

### Project Description

#### Purpose

The battery monitor board will ensure that the batteries connected to the rover will not be overused. Overusing Li-Po batteries can irreversibly damage them and potentially cause a fire.

#### Desired Behavior

- LED that indicates the voltage is good (22.2-24).
- Send a signal to the computer to indicate is it good or bad
  - Can either be digital (high for good or low for bad), or analog (0-5V range) where the computer does ADC to estimate the voltage

#### Pre-reqs

- Altium Knowledge
- Digital Logic
- Circuits 1

### Project Requirements

#### Size & Layout

TBD

#### Electrical I/O

- Takes in Battery (6s LiPo Battery)
- Outputs either a digital or analog signal to the computer
- LED indicator (On or Off)

### Optional Features

- LED Matrix that indicate a range

### Relevant Resources

TBD

RuAlMac, 2025-03-20:
03/20 Update: PCB design is done! Ready to order. Everything's been double-checked. I made some design changes last week: moved the LEDs to the top of the board so that they're visible once the board is installed in ReptileRover, also added a second fuse mount so that the board can be run at its rated maximum of 76A continuous / 80A instantaneous.

RuAlMac, 2025-04-07:
04/07: waiting for PCB and parts to be purchased. Wiki article completed.

Closed 2025-04-07.

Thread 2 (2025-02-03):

Motor driver

TheDinner22, 2025-02-03:
**Deadline: 04/01/2025**

### Project Description

We need the rover to move around!!!!

#### Purpose

Software will be able to interact with the DC motors and drive/turn the rover **through** this board.

#### Desired Behavior

- Speed driven by PWM (higher duty cycle, faster motors)
- some kind of digital logic kill system
- different PWN channels for left and right wheels
- each wheel has it's own enable

#### Pre-reqs

- Altium Knowledge
- Digital Logic
- Circuits 1

### Project Requirements

- the rover needs to be able to move!!

#### Size & Layout

TBD

#### Electrical I/O

- Takes in Battery (6s LiPo Battery)
- takes in ~6 different digital signals (enables for each wheel)
- takes in somewhere between 2 and 4 pwm channels from the PI

### Optional Features

- optimized to use only 2 PWM channels instead of 4
- heat monitor system or something with a temperature sensor??

### Relevant Resources

TBD

Shxl2, 2025-02-10:
This week, I spoke with @TheDinner22 about potentially adding encoders to the drive wheels for closed loop velocity control and wheel odometry.

I also discussed the possibility of adding an absolute encoder to the steer axis of the rover, so that it could be fully holonomic. With the way the rover is currently assembled, the steer motor is geared 1:1 so a motor with an integrated absolute encoder could be used, but I haven't been able to find one that's brushed.  An alternative could be to gear an external absolute encoder 1:1 with the steer, so that it could reset from any orientation, and ideally this encoder could also have a quadrature output for more accurate velocity readings. I've found one that fits these specifications, although admittedly it is a bit pricey and we'd need 4. [(https://store.ctr-electronics.com/products/srx-mag-encoder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)](url)

For steer, the other option that was discussed was a servo, which would be a lot easier to do electrically and mechanically (and a lot cheaper), but the odometry and control would suffer as a result, because there is no good way of telling where the motor is, you just have to believe that it's at the setpoint.

Regardless of what we do, we need to talk to the mechanical team so they can package the new motors and possibly encoders, and so they can figure out what to do with the wheel in the center, which cannot be on the ground while the rover is moving sideways. The motor driver boards would also need to change. The drive motors can't be controlled with just 2 outputs anymore, and more boards need to be made for the steering actuators.

TheDinner22, 2025-02-28:
leaving open but we have opted to use the following instead (at least for now):

https://www.handsontec.com/dataspecs/module/7A-160W%20motor%20control.pdf

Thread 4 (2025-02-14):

Software + ROS (maybe) + I2C for PI hat

TheDinner22, 2025-02-14:
**Deadline: 04/01/2025**

### Project Description

#### Purpose

PI needs to talk to some hat via I2C. We need software that does that. Ideally somewhat generic since this hat will be driving the DC
wheels and the servos that let the rover turn.

#### Desired Behavior

- only uses 3 pins for I2C
- minimal wiring to make use of the PI hit
- 16 different PWM channels with full use of the 12-bit channel resolution

#### Pre-reqs

- uP
- 3701C
- python
- PI sdk stuff

#### Size & Layout

- ideally you can do this with no extra wiring (excluding the wires to the motor)

#### Electrical I/O

- no extra wires pretty please

#### optional stuff

- maybe put ROS2 two on the PI?!?!?
- maybe a docker environment that mimics the PI's setup.

### Relevant Resources

[here's the hat](https://www.pishop.us/product/servo-driver-hat-for-raspberry-pi-16-channel-12-bit-i2c/)

Shxl2, 2025-02-17:
This week I worked on imaging the pi with Ubuntu 24.01 so that eventually we could put ROS2 Jazzy on it. For now, I'm looking into using docker to ease software development. What I want to do is use a local registry to push and pull docker images, and make a script file that will ssh into the pi and run said docker image. The intent is that anyone can pull the software repository, and with docker installed, can use the IDE of their preference (VSCode, Jetbrains, NeoVim, etc.) to build images, run a script that pulls that image onto the pi, and then run that image on the pi. Because the rover is meant for newer members to work on, I want to make the software development process as simple as possible. To do this, I'm currently learning how to use docker and make local registries. I'm going to talk to some of the software leads about this to see if they have any advice.

Here's one of the resources I'm looking at: [https://docs.docker.com/get-started/docker-concepts/the-basics/what-is-a-registry/](url)

Because the pi is running Ubuntu (either via docker or with the imaged os) for ROS, we need to use a different GPIO library that on raspberry pi os. The library that is recommended for Ubuntu is LGPIO according to this website: [https://ubuntu.com/tutorials/gpio-on-raspberry-pi#2-installing-gpio](url) This guide goes through how to interface with basic gpio functionalities, i2c, and pwm. I plan on using this library to interface with the pi hat and control all of the actuators.

TheDinner22, 2025-02-23:
### Joe Handsome

PI hat came in this week and I got it working on Ubuntu. All of the code is in the NewCode2025 repo. We can control each of the 16 PWM channel's with functions (and we get to choose the duty cycle). There's also a version for driving servos.

This issue will likely be closed Monday or Tuesday since the code is super duper close to done (lowk will take me 5 min on Monday or Tuesday).

here's a video of one of the wheels being turned. We should be able to have the whole rover moving around by end of next week.

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

TheDinner22, 2025-02-28:
The code worked and the rover moves!!

Bugs
- turning is inverted (oops)
- code is poorly written (no loops and somehow I'm passing in negative PWM??)
- no graceful shutdown so rover tends to stay running after program is killed
- no ros2 launch so it's sort of involved to spin it up

Closed 2025-02-28.

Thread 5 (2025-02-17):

Servo motor + footprint+ meche

TheDinner22, 2025-02-17:
**Deadline: 04/01/2025**

### Project Description

#### Purpose

We need to pick some kind of 12V or 24V servo motor for the rover. We will need 4 in total.

#### Desired Behavior

Either the servos will work as a drop in replacement for the DC motors that are currently on the rover (same size/mounting mechanism).
OR
Ensure that the servos you pick can be mounted to the rover (pretty please)

### Project Requirements

servos end up on the rover and work to turn the front and back wheels.

#### Size & Layout

TODO

#### Electrical I/O

Try and get 24V servos. 12V servos will require a buck converter.

#### Project Tasks

choose motors
order motors
mount motors

Shxl2, 2025-02-20:
The servo that the mech team is looking into is the Axon mini. [https://axon-robotics.com/products/mini](url) This servo was designed for FIRST Tech Challenge and due to it's design constraints, it has an analog absolute encoder output. We could use this to reset the azimuth upon initialization no matter what orientation it's in. This is a 12V servo so we're gonna have to buck boost down to 12V. The mounting solution is still a WIP.

SzanderB, 2025-03-02:
Quick summary about using Pi Picos as Quadrature Decoders
Purpose: Use a Pico to do quadrature decoding for hopefully 8 motors
Background: [This link](https://forums.raspberrypi.com/viewtopic.php?t=346174) shows a pico handling 8 encoders and then transmitting them via I2C or SPI. Source code is found through the github link in both python and C/C++
Using Programmable Input Output, there are 8 slots in which we can receive encoder data, send to main CPUs, then analyze and send in packets to host Raspberry Pi when needed.
Quick Intro to [PIO](https://www.youtube.com/watch?v=YafifJLNr6I&ab_channel=LifewithDavid)
[YT](https://www.youtube.com/watch?v=jklc2Aq9-1E&ab_channel=XtendedGreg) and [Github](https://gist.github.com/XtendedGreg/83f1c23f43f8bda27ad761195160fbdd) link to a working quadrature decoder in MicroPython. I’d recommend only using this to get one operational. If we need to do 8, micropython might not be good enough.

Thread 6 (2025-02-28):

Pi and driver hats for anti rats nest

TheDinner22, 2025-02-28:
**Deadline: 04/01/2025** (lowk b4 spring break plz)

### Project Description

There is a horrible routing wiring rats nest issue. Most of the boards we are working with rn have male [dupont-like](https://en.wikipedia.org/wiki/Pin_header) connectors

#### Purpose

Standardize connections and make it so that the person wiring up the rover doesn't need to understand where each individual wire goes.

Ideally we will have hats for the pi and the 3 motor drivers.

#### Desired Behavior

Pi hat and motor driver hats should break the respective pins out to [sherlock](https://www.digikey.com/en/product-highlight/m/molex-connector/sherlock-connector-system) connectors.

The sherlock connectors should be labeled ***so that someone connecting them can easily tell which cable goes where***

#### Pre-reqs

- Altium tutorial

### Project Requirements

pins should also be forwarded so that we can stack hats on top of your hat if desired.

#### Size & Layout

Pi and motor drivers are in lab. There are also probably several Pi hat-templates online.

#### Electrical I/O

These are all low voltage signals and your board doesn't need to worry about power, ground, or noise.

### Relevant Resources

I will add the spec here in like 40 minutes

hannahc963, 2025-03-03:
Got assigned to and started working on this task on Friday 2/28. So far I have an Altium project with a PI hat and am working on the PI hat connections to the sherlock connectors.

hannahc963, 2025-03-10:
Have schematic for PI hat done and am working on the PCB layout. Should be able to finish the motor driver hats as well by this Friday.

hannahc963, 2025-03-16:
3/16: Finished PCB layout for PI hat and finished schematic and PCB layout for motor driver hats. Will push two Altium projects into branch pi-driver-hats-2025 by end of today.

hannahc963, 2025-03-31:
3/30:
Made some final edits:
- Added pours for GND and Power
- Cut Pi Hat in half
- Labels and Logo
- Note: Rules not imported to projects

hannahc963, 2025-04-07:
4/6:
Adrian and Joe looked over my boards and they should be ordered soon.

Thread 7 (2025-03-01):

Sonar with I2C and pico

TheDinner22, 2025-03-01:
**Deadline: 04/01/2025** (b4 spring break plz)

### Project Description

I made a branch for ur code called `sonar_pico_code` (empty rn ofc)

we have these sonar things. Pretty please have the pico constantly ping them and provide the data over I2C when requested. Do the processing on the PICO, so data should be in cm or something similar.

#### Purpose

The use of a pico will free the pi up to do anything else (probably ros stuff).

#### Desired Behavior

PICO abstracts all information about the sonar(s) away and simply provides data over I2C when requested.

#### Pre-reqs

- PICO experience
- uP
- I2C
- DAD (for understanding how the sonar works maybe ig)

### Project Requirements

#### Size & Layout

Ideally we'd have a small custom pcb for this. However, I think we'll want to modify what the PICO is doing and possibly use it for more in the future. This task is more about the embedded code. ***Just get it working on a breadboard pretty please***.

#### Electrical I/O

4 pins to the sonar (per sonar)
3 pins to the pi (I2C pin-count independent of the number of sonar).[

### Relevant Resources

pretty sure [this](https://www.digikey.com/en/products/detail/sparkfun-electronics/SEN-24049/22258319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) is the exact part.

JakeWesta, 2025-03-10:
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

Got the sonar working with connecting to the Pico. Sir Handsome and I will work on Monday to take a running average and transmit that to the PI with I2C, should be chill. Heres the wiki page that im dumping some info on. https://milwiki.cbrxyz.com/wiki/HC-SRO4_Sonar

JakeWesta, 2025-03-15:
3/10-3/17:
- In NewCode2025 branch, joe and i worked on making sonar_master, which is a ROS node that takes the sonar code i wrote (revised into python) and publishes it so that it can be listened to.
- We tried to get I2C working from pico to pi but it was not being nice, so thats why we switched to a ROS node and directly connected to pi.

JakeWesta, 2025-04-07:
3/31-4/7:
- (Technically not the issue I'm on but it doesnt really have a github, besides the point)
- Tested the sonar's detection capabilities mildly extensively for a couple of hours, it CAN work but it is really not optimal, therefore I looked elsewhere and did research on sonar microphones and transducers to see what capabilities are out there that can suit our needs. Going to talk to Sir Lester and Joe about it to see what they think. Awesome.

JakeWesta, 2025-04-14:
4/8-4/13:
- Looked into RobotX description of the challenge (https://robonation.org/app/uploads/sites/2/2024/09/2024-RobotX_Team-Handbook_v1.0.pdf), Page 19) to understand what I would want to model in the rover itself.
- https://micbooster.com/ultrasonic-microphones/146-ultrasonic-mic-board.html shows decent promise, however I am worried with range and the fact that it would require extra post processing and filtering.
- [this one](https://maxbotix.com/products/mb1340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) is also a solid option.
- ive learned that land based sensor suck with distance so it will be hard to replicate the RobotX challenge well, perhaps scaling down the course would help and be still be valid.
- Had a rough week, but life is good this week and will lock in decisions tomorrow at the meeting.

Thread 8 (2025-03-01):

IMU + pi connection

TheDinner22, 2025-03-01:
**Deadline: 04/01/2025** (by Friday the 7th)

### Project Description

Lorant was kind enough to give me an IMU!!! We need a ros lib/node to publish IMU data to a topic. Specifically, we need the rotational data (the IMU is going to be a compass).

#### Purpose

We want the rover to be able to turn 90 degrees or 80 degrees or whatever number. The motors are open loop so we need something else to tell us how much we have turned. The IMU will give us an absolute output.

#### Desired Behavior

IMU working with the PI over usb (and powered over usb too). Working ros2 lib for the IMU.

#### Pre-reqs

- uP
- ros2
- RASPI

#### Size & Layout

Do NOT put the IMU near any current carrying wires since the induced magnetic field will mess with the compass output.

#### Electrical I/O

All connections over USB directly to the PI.

### Relevant Resources

maybe port [this](https://github.com/vortexntnu/stim300-driver) to ros2.

[here's](https://safran-navigation-timing.com/wp-content/uploads/2022/12/STIM300-Datasheet.pdf) the datasheet

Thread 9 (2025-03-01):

autonomous rover v1, integration

TheDinner22, 2025-03-01:
**Deadline: 04/01/2025**

Lowk we can't start this until the sub issues are done :(

### Project Description

Integrate the Pi hat, IMU, and sonar to make the rover drive autonomously.

#### Purpose

This will be a ros node in mil2/src/reptilerover/mission_control that handles data from the sonar and IMU and uses that data to drive to motors.

#### Desired Behavior

Rover should literally just drive forward until the sonar detects something, then turn away from that thing and keep driving. Also the xbox controller should drive the rover with a higher priority than the sonar.

#### Pre-reqs

- ros2

#### Electrical I/O

Ideally this won't require additional wiring since the integration is in ros2/software.

#### Project Tasks

IMU + pi connection
Sonar with I2C and pico
Pi and driver hats for anti rats nest

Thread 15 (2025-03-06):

Rover GPS Module - GPS Data

LesterBonilla, 2025-03-06:
# Description
Not a lot is known about the current GPS module. Look up the part and talk to a Rover leader about it. Get it working and getting data for this issue.

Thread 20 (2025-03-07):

Rover Camera Integration

LesterBonilla, 2025-03-07:
# Description
We have a [camera](https://shop.luxonis.com/products/oak-d-w)! We need to decide how to integrate this into the Rover and get its data. The camera has on-board image processing/AI acceleration that we need to look into.

# Deliverables
A quick report on what you've learned about the camera
An idea of how you suggest we integrate the camera (I.E. how to implement a vision model on it). We can ask the software team member to work with you on this task.
A ROS node that will stream data from the camera.

SzanderB, 2025-03-13:
https://docs.google.com/document/d/1AMI41eQ0rKKQh_LzfCIfXSjAarU053IaULmf-sOdI7E/edit?usp=sharing

Doc for writing down findings^^ Will transfer over to wiki after were done

nollfrt, 2025-03-14:
Assigning myself to this issue

SzanderB, 2025-04-04:
Week of 3/31: Got camera ros node operational when connected to computer. Code is found in github linked in Wiki Page. Library includes template code for posting raw image data, rgb data, as well as stereo data. Worked on understanding how to use the on board AI acceleration for neural net models for use in recognizing buoys. Minorly edited the Wiki Page. Next steps are editing the Wiki Page to look much better as well as getting a working buoy recognizor model on the camera.

SzanderB, 2025-04-14:
Week of 4/7: Was out for beginning of week and got sick for a few days. Didn't put too much time in but got pictures of buoy and attempted to use MIL computer to make a PyTorch Model for object detection. Computer was broken, so tried doing it on my laptop and could not get label studio to install correctly. Ran out of time, but next week is update wiki and get a model working.

nollfrt, 2025-04-14:
Week of 4/7: Made minor edits to the wiki (added infobox) and began studying and researching how to implement an AI model

SzanderB, 2025-04-20:
Got label-maker to work, labeled buoy image data, got bounding box label info, downloaded ultralytics to train yolo model, trained model, now need to convert to a file type that works with the camera and upload the code

nollfrt, 2025-04-21:
Continued trying to implement AI model. Szander got one to work and was able to train it, so now looking into converting it to a file type compatible with the camera.

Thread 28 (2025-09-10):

[Mechanical] Figure out how to mount the ball launcher to the rover

RuAlMac, 2025-09-10:
**Deadline: 10/31/2025**

### Project Description
We need to mount the ball launcher onto the rover. Eventually, we'll be making a new chassis for the rover. For the time being, we just need to identify what is needed to securely mount the ball launcher. We also need to be sure it won't fall off the rover when it is operating.

#### Purpose
To mount the ball launcher to the rover.

#### Desired Behavior
Ball launcher doesn't fall off the rover (or cause the rover to flip over) when the rover is moving, when the ball launcher is firing, etc.)

#### Pre-reqs
- CAD experience

### Project Requirements

#### Size & Layout
- The mounting system for the ball launcher should not be super heavy. More than likely, the next chassis for the rover will also be made out of acrylic, so this mount needs to be sturdy enough to support the launcher while also not shattering the acrylic chassis.

#### Electrical I/O
Remember to take into account the wires coming out of the ball launcher. We'll need to direct these wires to the inside of the chassis, so make sure to leave space for them! Cable management would also be nice.

### Optional Features
- Would be nice if it were easy to mount/dismount the ball launcher from the rover.
- Also ball storage? Balls will be manually loaded into the ball launcher, but if they could be stored onboard the rover, that would be pretty cool.

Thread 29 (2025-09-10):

[Software] Programming rover!

RuAlMac, 2025-09-10:
**Deadline: 10/31/2025**

### Project Description
We need to write software for the rover. There's lots to do!
- Get Raspberry Pi 5 talking with the Cube Pilot Orange+ sensor hub
- Get Raspberry Pi 5 talking with the RFDx900 radio modem
- Get Raspberry Pi 5 talking with a stereo camera for future machine vision capabilities
- Get controller talking with Pi 5 for manual rover control
- Make it easy to program in future onboard sensors for collision prevention (e.g., several ultrasonic sensors mounted to the outside of the rover to detect if there is a wall approaching)
- Make it easy to program in future sensors for color detection (e.g., a color sensor mounted to the bottom of the rover so that the rover can follow a track on the ground)

#### Purpose
The first priority with this rover is to get it moving at all. That means getting the Pi 5 talking to a controller should be the first task to get done. Past that though, this rover is kind of an open book. We don't have any hard and fast requirements since we're not competing with it, so we can just kind of do whatever we want.

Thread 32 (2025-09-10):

[Mechanical] Designing mount for E-Stop Button

RuAlMac, 2025-09-10:
**Deadline: 10/31/2025**

### Project Description
We have an E-Stop button that will be mounted on the rover to instantly kill the motors if needed. This button is a bit large and needs to be mounted on top of the rover (or somewhere else where it is easily accessible). We need to design a mount to hold this button in place.

#### Purpose
The E-Stop is a safety device and is very important if something bad starts happening with the motors.

#### Desired Behavior
We're planning to have this mount 3D printed, so design accordingly. It can come in multiple parts if needed, but the simpler the better. The E-Stop is designed to be smacked if needed. The mount needs to also be able to take a heavy smack, and should not break even if the E-Stop is hit pretty hard (within reason of course).

#### Pre-reqs
- CAD experience

### Project Requirements
Deliverable: a solid 3D printed mount for an E-Stop button (we already have the button, just need to design a mount for it).

#### Size & Layout
This mount shouldn't be huge! It will be mounted onto the chassis somehow, so coordinate with other MIL members working on the chassis.

#### Electrical I/O
There will be (at least) two wires connected to the button. Design the mount accordingly. We need easy access to the terminals of the battery, but the terminals should also be shielded so that a stray piece of metal won't short them.

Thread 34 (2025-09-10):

[Electrical] Sensors for collision detection

RuAlMac, 2025-09-10:
**Deadline: 10/31/2025**

### Project Description
Currently, the rover has no way of knowing if it is about to run straight into a wall. In the past, we had an ultrasonic sensor attached to the front of the rover for this purpose. If the rover was approaching a wall, this sensor would detect that and tell the rover to stop or change direction. We want to restore this functionality, but do so more comprehensively.

We want to attach ultrasonic (or some other kind of distance sensor) to each side of the rover (front, back, left, right). These sensors will communicate with the Raspberry Pi 5 to alert the rover of an imminent collision. We also want to make sure that sensors are mounted securely to the chassis, and have a good electrical connection to the Pi. One idea to ensure this is designing a small PCB that a sensor can be mounted to.

#### Definitions
- Ultrasonic sensor: a type of distance sensor. This sensor shoots out a wave of sound at a frequency not audible for humans, and determines distance from an object based on how long it takes for the sound to reflect back.

#### Purpose
Securely mounting sensors to the sides of the rover for collision detection and prevention.

### Project Requirements
- Choose a type of sensor that can be used to detect distance from walls / other objects. This sensor should be small, not super power intensive, and not super expensive.
- Design a PCB that this sensor can be mounted to. Nothing too crazy, just a simple mounting board for our sensors.
- Determine how these sensors will connect to the Raspberry Pi 5 onboard the rover. Will they use a communication scheme (I2C, SPI, etc.)? Do they have an analog output that varies based on distance from an object?

#### Size & Layout
The PCB mount for these sensors should be quite small. Ideally, less than 20x20mm.
Also make sure to put a good connector on this PCB! We don't want to just use header pins / Dupont wires because those do not always provide a good electrical connection. Screw terminals, shrouded headers, Sherlock connectors, etc. are good options.

Once this project is completed, it will be handed off to the mechanical team. They will design a mount for your sensor PCB to be mounted to the chassis.

aouress, 2025-09-24:
Decided to use the VL53L4ED ToF sensor from STMelectronics because it had better mid-to-close range accuracy than the TL53L0X. The first version of the board is complete. Once reviewed, I'll make a wiki page for all the information related to the ToF sensor and breakout board.

aouress, 2025-10-05:
The board is complete and BOM has been uploaded to the repo. Should be good to order whenever we want.

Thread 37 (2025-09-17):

[Mechanical] Revise ball launcher mechanism to shoot one ball at once

RuAlMac, 2025-09-17:
**Deadline: ??**

### Project Description
Currently, the ball launcher will sometimes shoot two balls at once. Ideally, the launcher should only shoot one per "shoot" command sent. The issue is that the part that drops balls onto the spinning flywheel is too short / ineffective. We need someone to redesign this part (or at least modify it) so that only one ball hits the flywheel at once (and gets shot out).

#### Purpose
To get the ball launcher operating as planned.

#### Desired Behavior
Ball launcher shoots one ball per "shoot" command instead of one/two.

#### Pre-reqs
N/A

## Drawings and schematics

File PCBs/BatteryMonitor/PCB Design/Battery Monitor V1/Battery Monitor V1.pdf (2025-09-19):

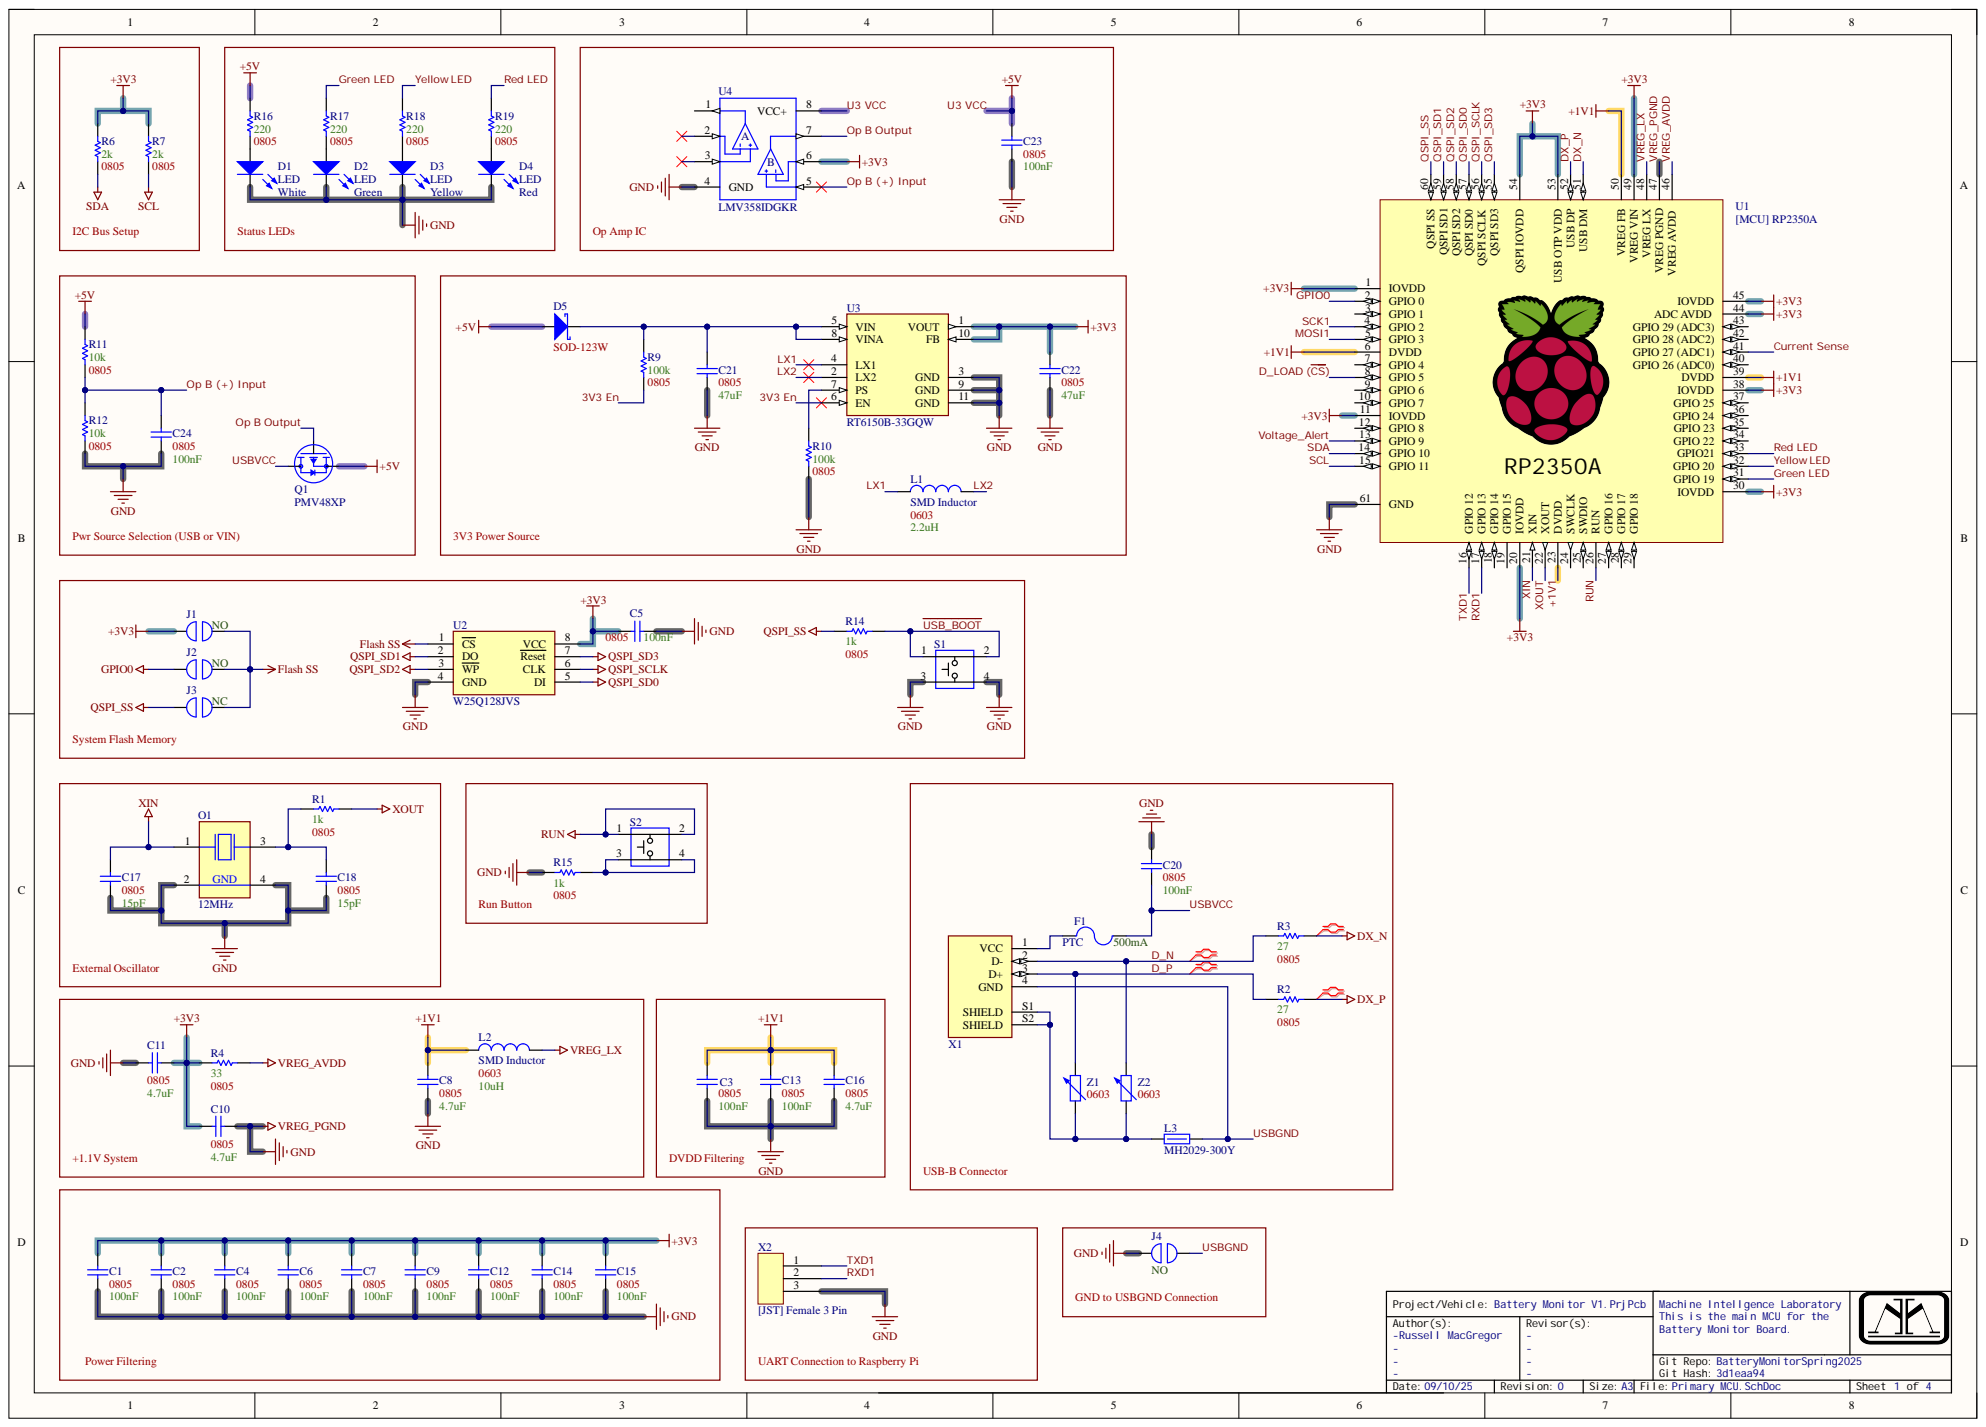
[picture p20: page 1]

QSPI SD3 55 QSPI SCLK 56 QSPI SD0 57 QSPI SD2 58 QSPI SD1 59 QSPI SS 60

USB DM 51 USB DP 52 USB OTP VDD 53

VREG AVDD 46 VREG PGND 47 VREG LX 48 VREG VIN 49 VREG FB 50

Pwr Source Selection (USB or VIN)

GND to USBGND Connection

Machine Intellgence Laboratory
This is the main MCU for the
Battery Monitor Board.

UART Connection to Raspberry Pi

Git Repo:
Git Hash: 3d1eaa94
File:Primary MCU.SchDoc

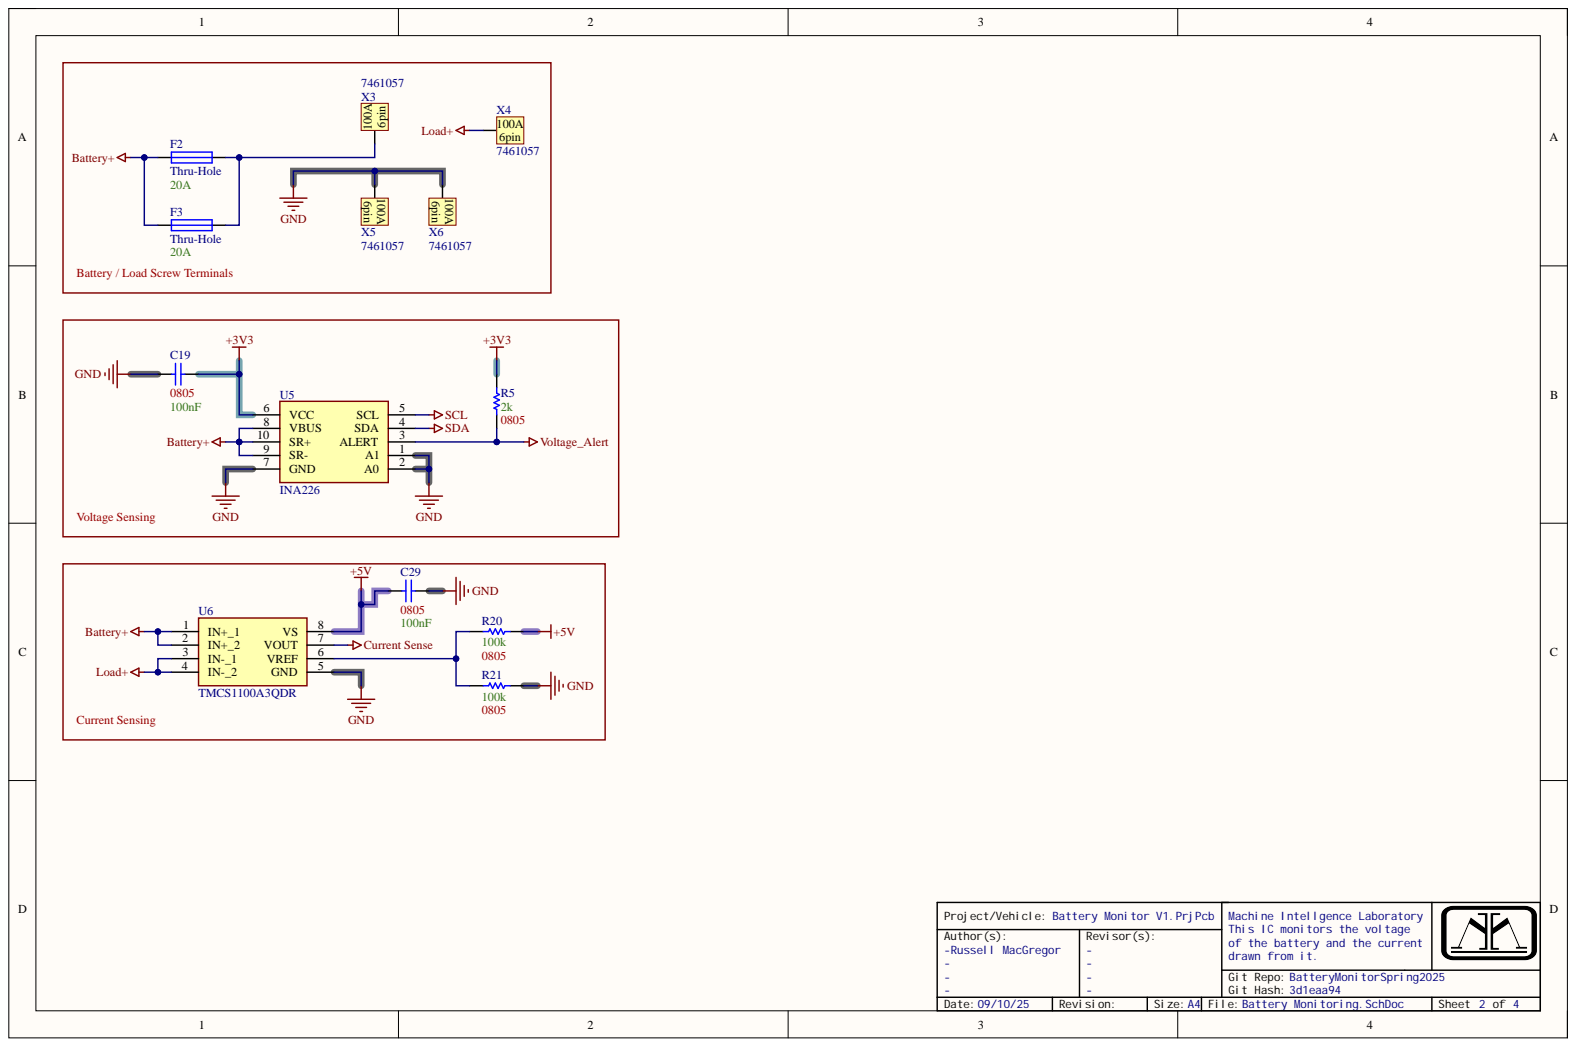
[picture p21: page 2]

Battery / Load Screw Terminals

Project/Vehicle: Battery Monitor V1.PrjPcb | Machine Intellgence Laboratory This IC monitors the voltage of the battery and the current drawn from it.
Author(s): -Russell MacGregor --- | Revisor(s): ----

Date:09/10/25 | Revision: | Size:A4 | File:Battery Monitoring.SchDoc | Sheet 2 of 4

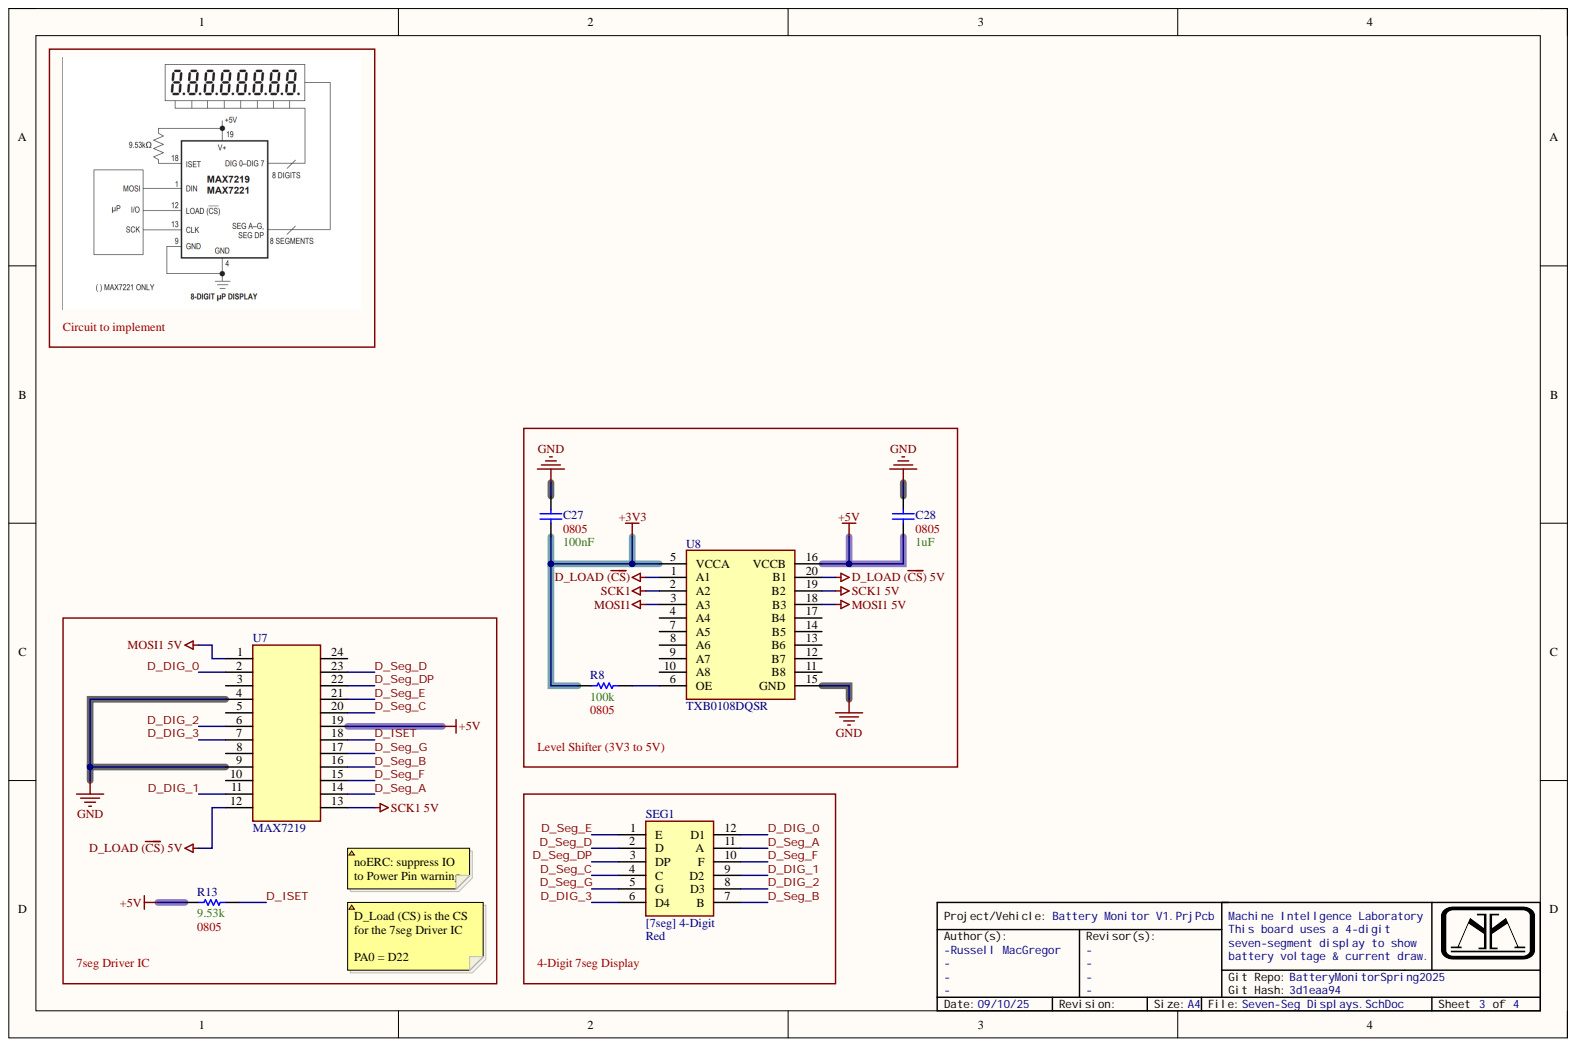
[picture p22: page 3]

noERC: suppress IO
to Power Pin warning

D_Load (CS) is the CS
for the 7seg Driver IC PA0 = D22

P r oj e c t / Ve h i c l e : Ba t t e r y Mo n i t o r V 1 . P r j Pc b | Ma c h i n e I n t e l l g e n c e L a b o r a t o r y T h i s b o a r d u s e s a 4 -d i g i t s e v e n -s e g me n t d i s p l a y t o s h ow b a t t e r y v o l t a g e & c u r r e n t d r a w.
A u t h o r ( s ) : ----R u s s e l l Ma c Gr e g o r | Re v i s o r ( s ) : ----

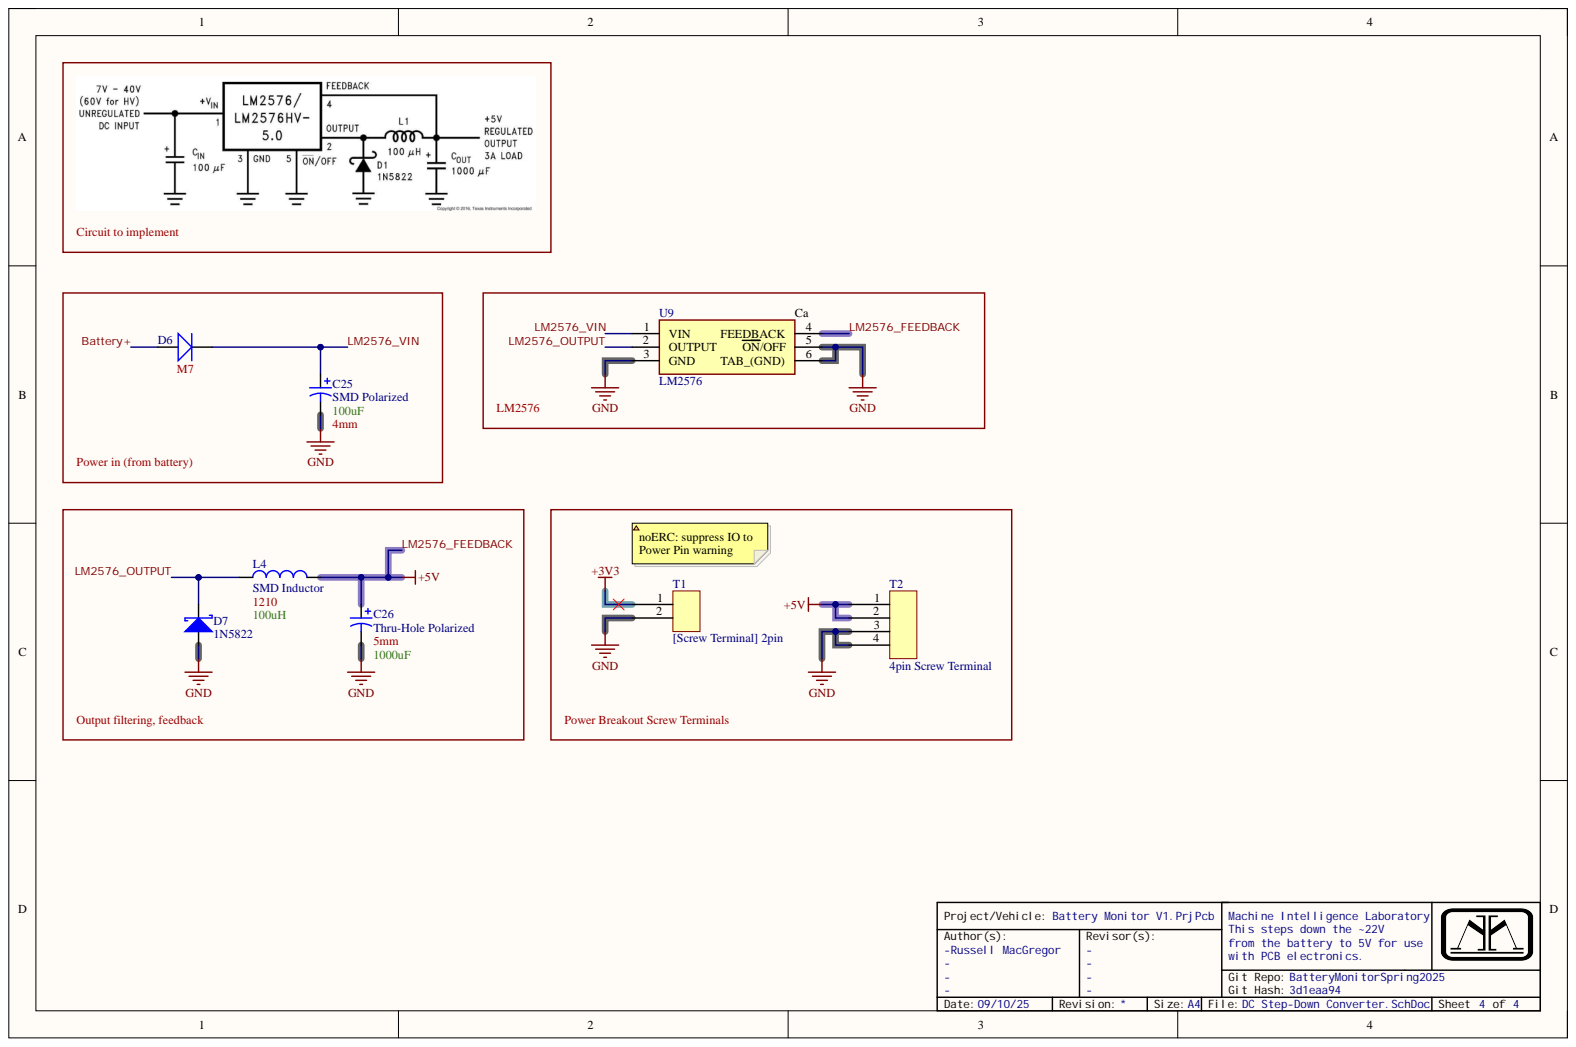
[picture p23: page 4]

Power in (from battery)

noERC: suppress IO to
Power Pin warning

Power Breakout Screw Terminals

Project/Vehicle: Battery Monitor V1.PrjPcb | Machine Intelligence Laboratory This steps down the ~22V from the battery to 5V for use with PCB electronics.
Author(s): -Russell MacGregor --- | Revisor(s): ----

Date:09/10/25 | Revision: * | Size:A4 | File:DC Step-Down Converter.SchDoc | Sheet 4 of 4

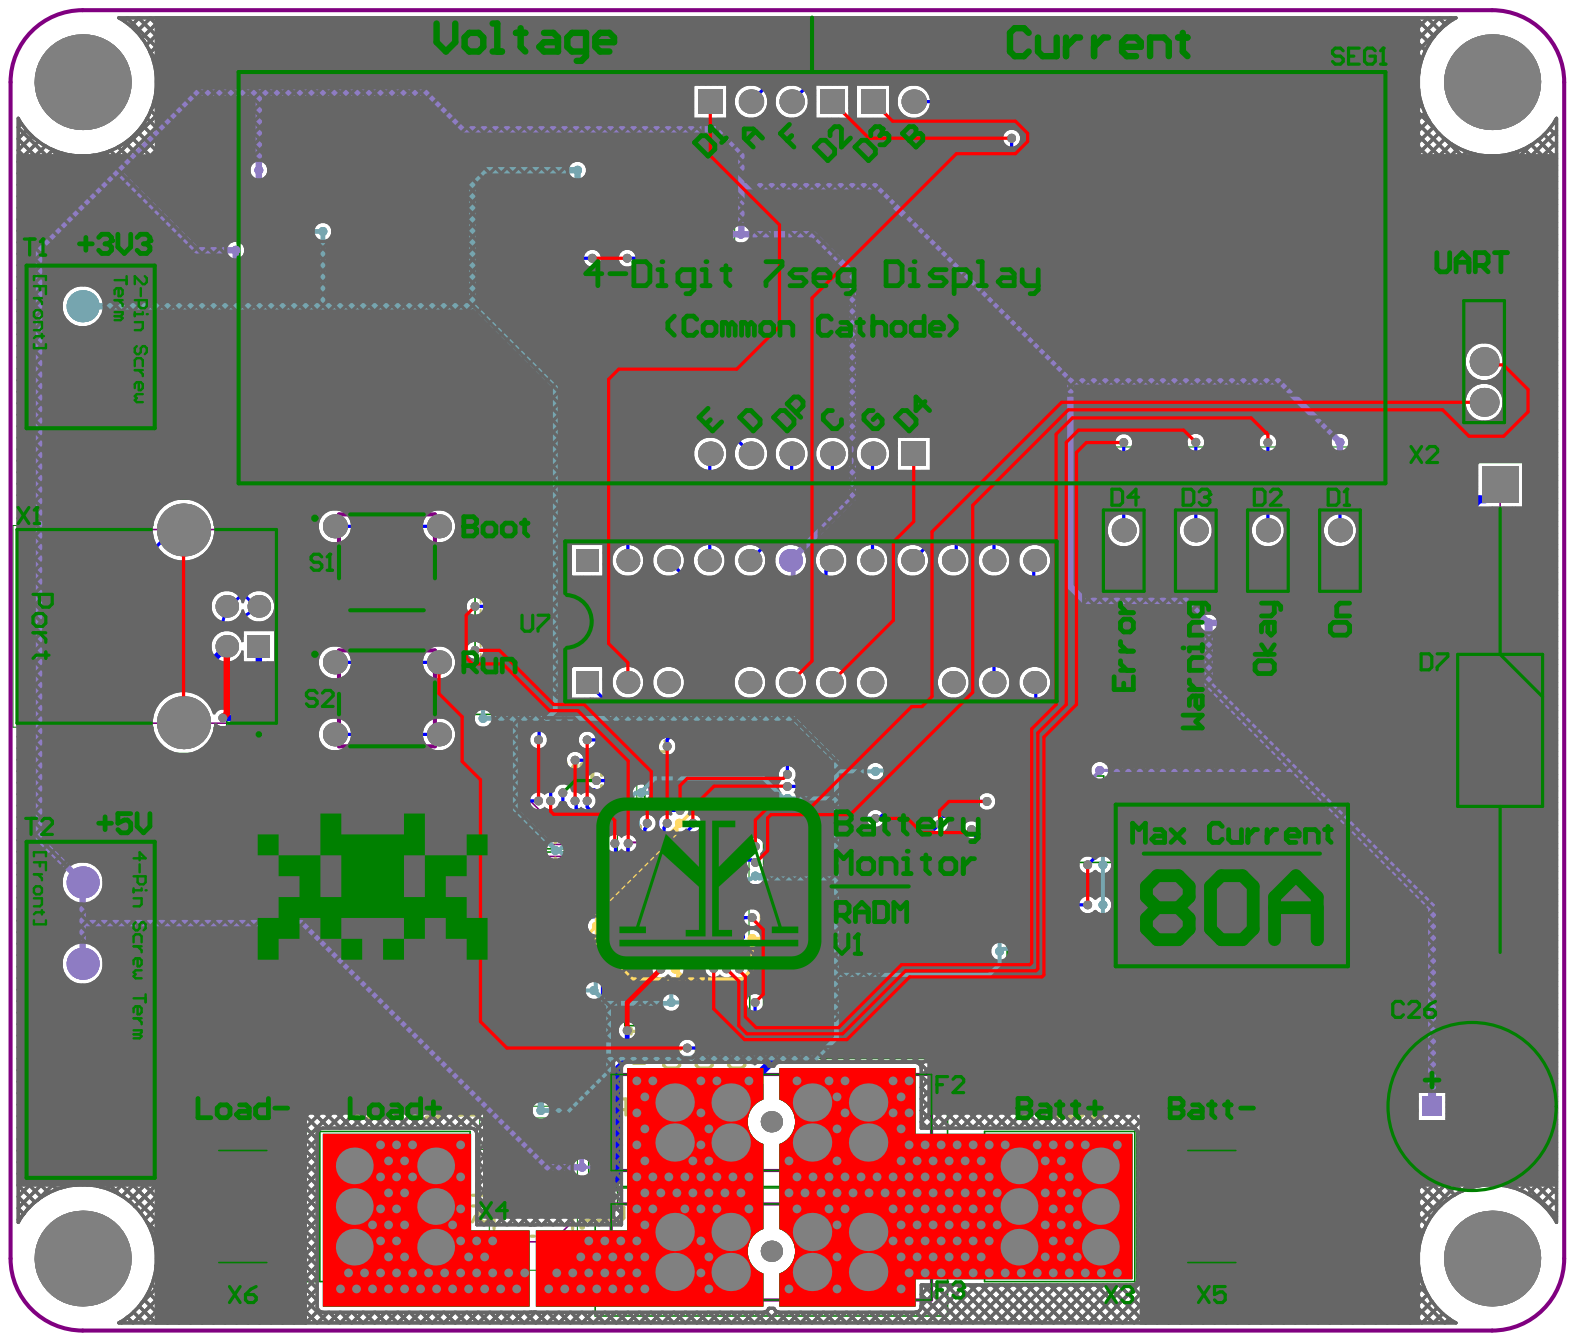
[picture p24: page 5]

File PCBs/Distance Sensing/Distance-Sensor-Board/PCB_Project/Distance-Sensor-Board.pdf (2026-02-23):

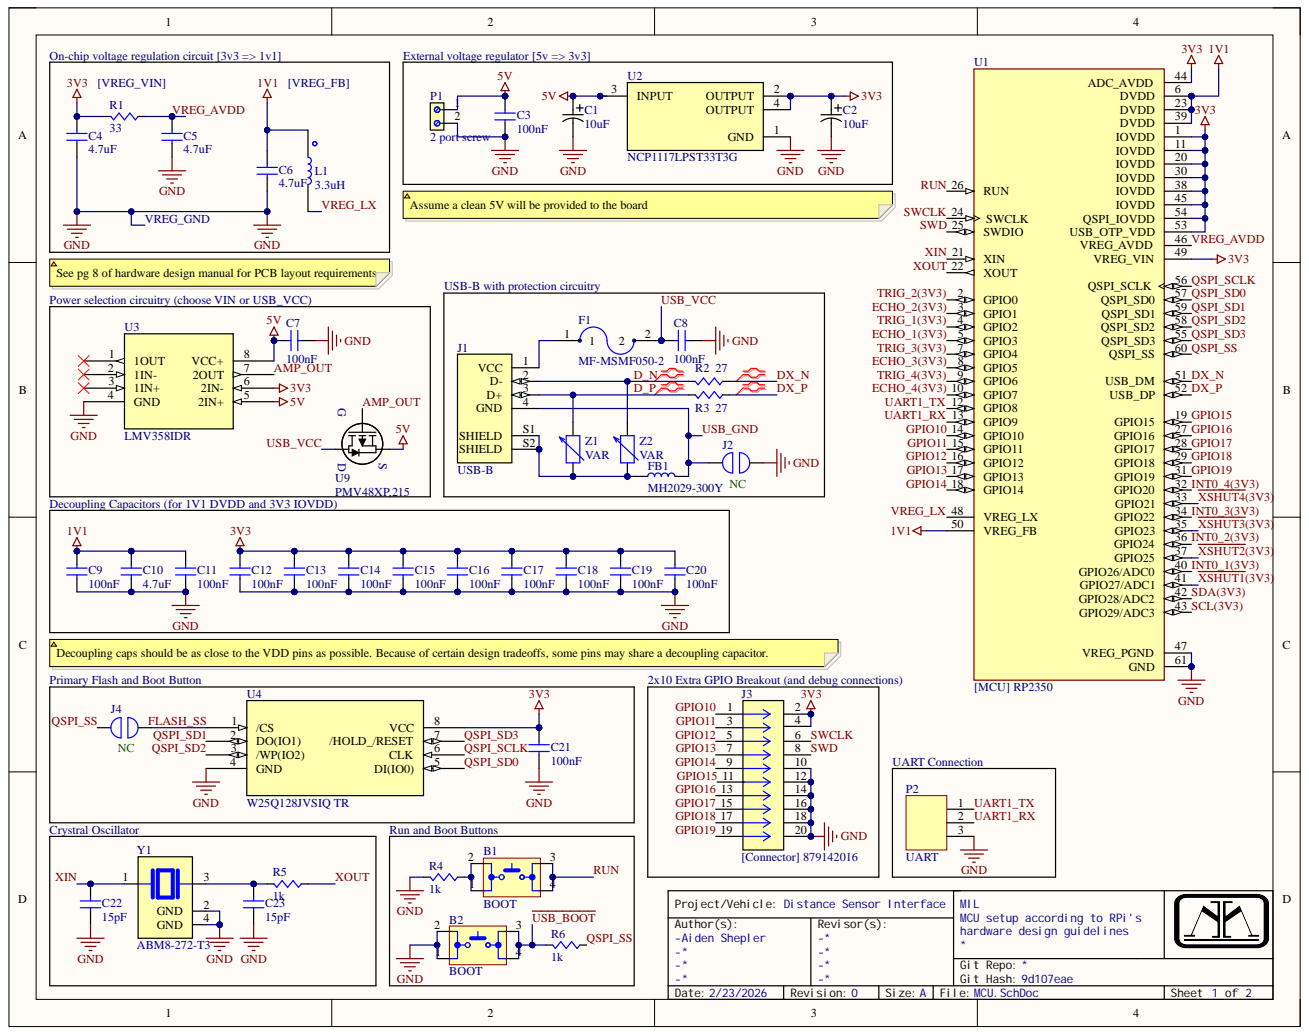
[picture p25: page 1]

On-chip voltage regulation circuit [3v3 => 1v1]

Assume a clean 5V will be provided to the board

See pg 8 of hardware design manual for PCB layout requirements

USB-B with protection circuitry

Power selection circuitry (choose VIN or USB_VCC)

Decoupling Capacitors (for 1V1 DVDD and 3V3 IOVDD)

Decoupling caps should be as close to the VDD pins as possible. Because of certain design tradeoffs, some pins may share a decoupling capacitor.

Primary Flash and Boot Button

2x10 Extra GPIO Breakout (and debug connections)

Run and Boot Buttons

Project/Vehicle: Distance Sensor Interface | MIL MCU setup according to RPi's hardware design guidelines *
Author(s): -Aiden Shepler -* -* -* | Revisor(s): -* -* -* -*

Date: 2/23/2026 | Revision: 0 | Size: A | File: MCU.SchDoc | Sheet 1 of 2

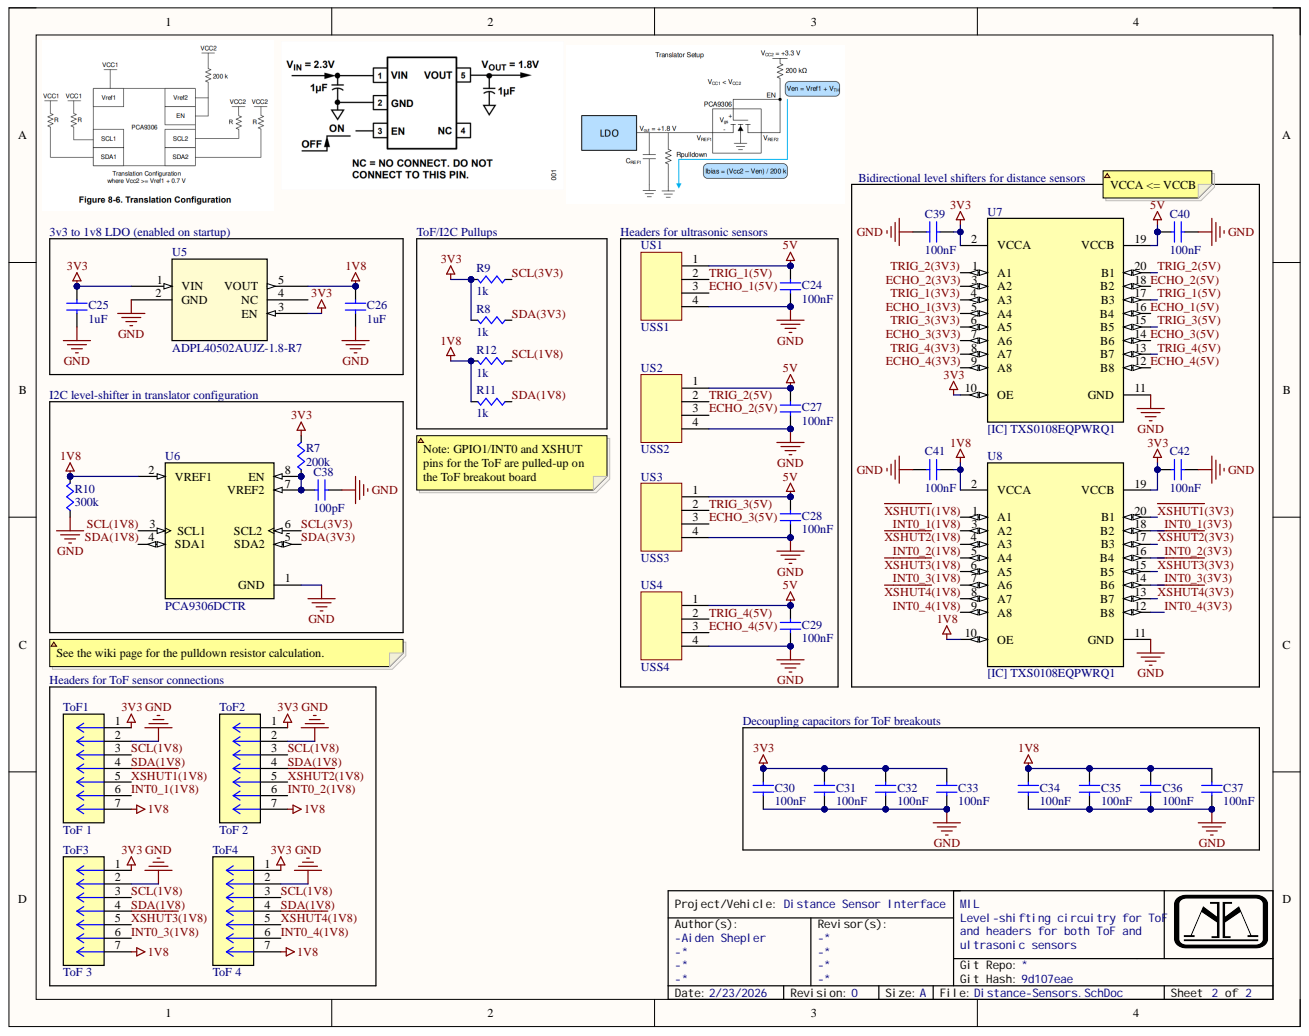
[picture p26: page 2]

aders for ul
SCL(3V3) SDA(3V3) SCL(1V8) SDA(1V8)

Project/Vehicle: Distance Sensor Interface | MIL Level-shifting circuitry for ToF and headers for both ToF and ultrasonic sensors
Author(s): Aiden Shepler *** | Revisor(s): --------****

Date: 2/23/2026 | Revision: 0 | Size: A | File: Distance-Sensors.SchDoc | Sheet 2 of 2

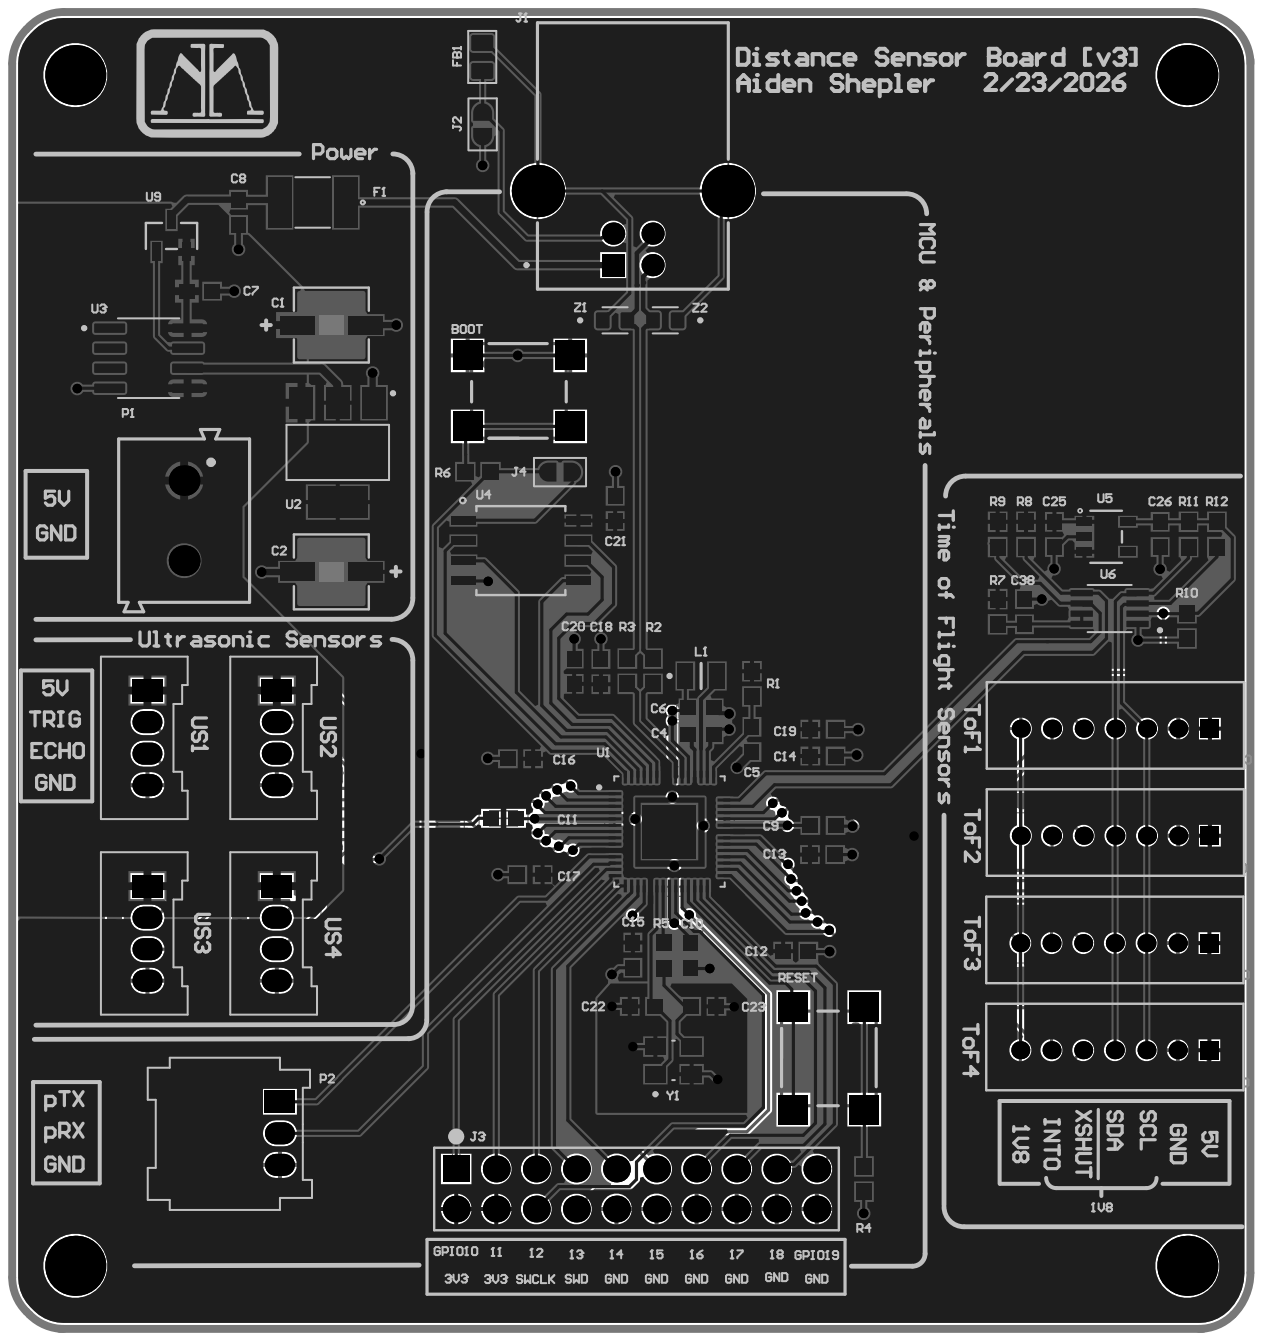
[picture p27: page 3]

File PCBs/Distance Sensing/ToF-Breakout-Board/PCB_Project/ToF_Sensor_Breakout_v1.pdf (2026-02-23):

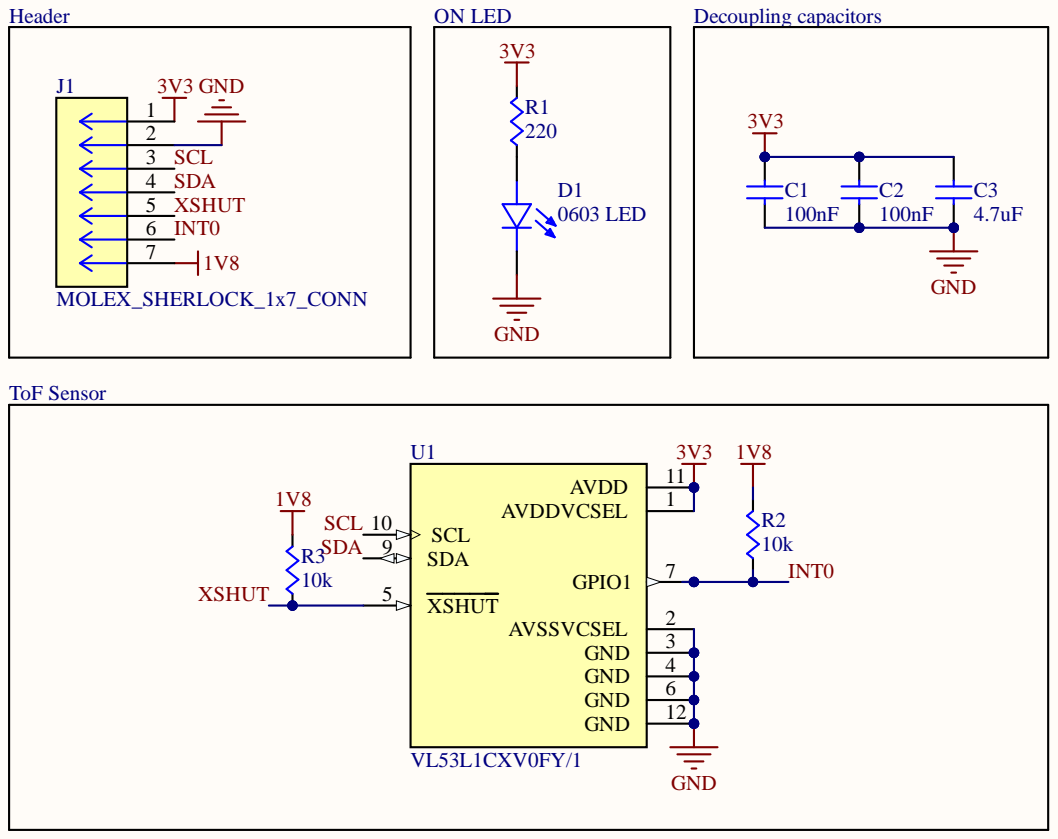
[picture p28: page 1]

Project/Vehicle: ToF Breakout Board | * *
Author(s): -Aiden Shepler --- | Revisor(s): ----

TerraGator/ToF-breakout-board

Date: 2/23/2026 | Revision: 0 | Size: A | File: main.SchDoc | Sheet 1 of 1

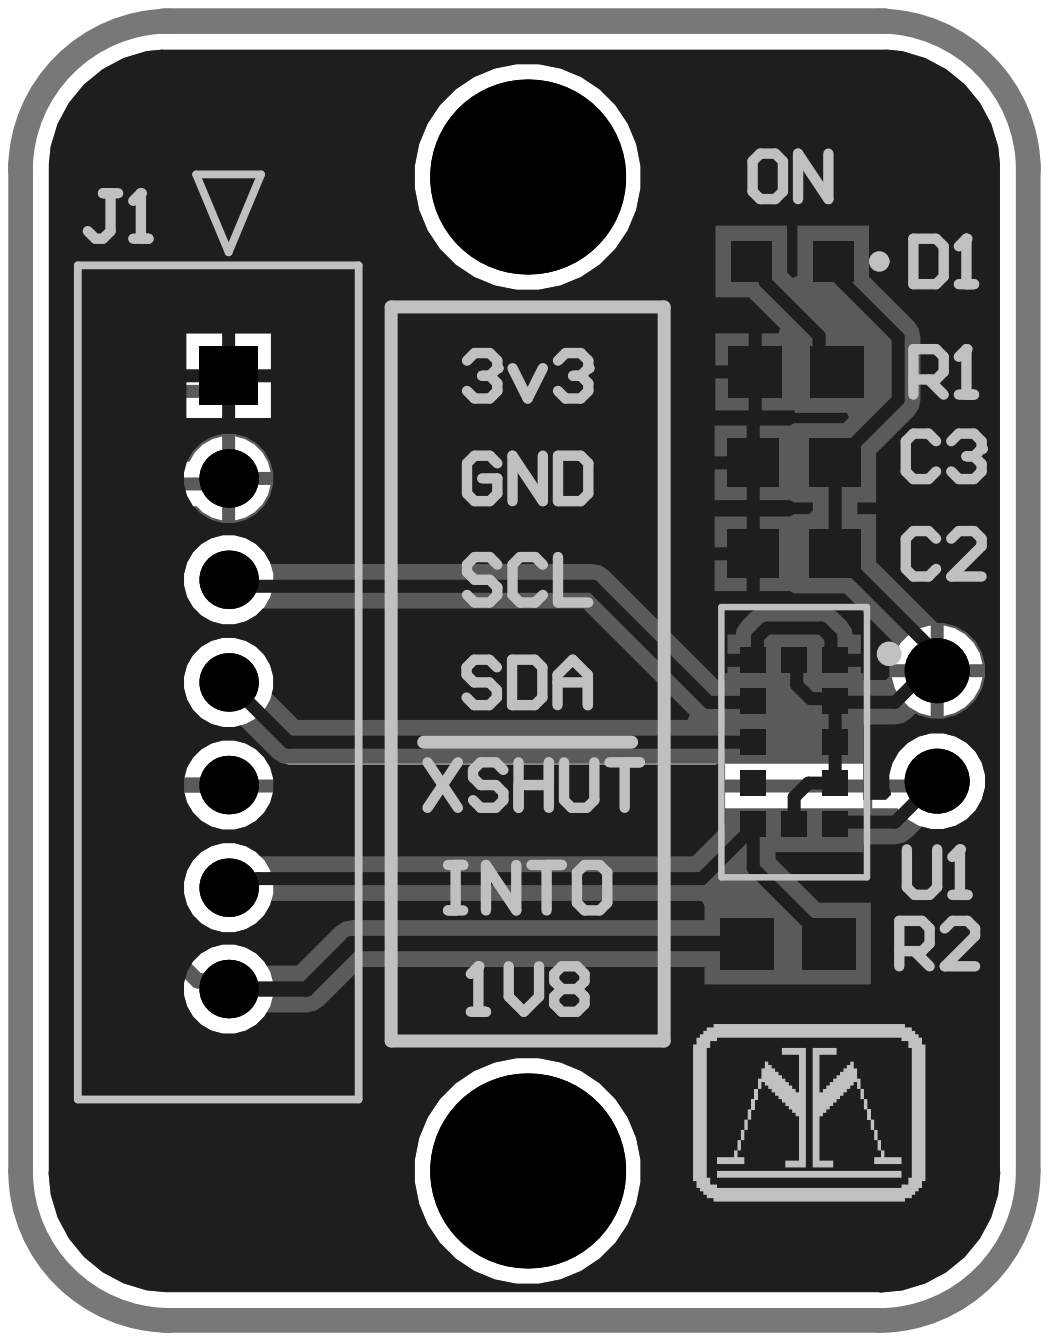
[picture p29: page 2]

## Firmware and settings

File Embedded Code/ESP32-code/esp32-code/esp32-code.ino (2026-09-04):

/**********<Dependencies>**********/
// I2C
#include <Wire.h>

// RemoteXY
#define REMOTEXY_MODE__ESP32CORE_BLE
#include <BLEDevice.h>
#define REMOTEXY_BLUETOOTH_NAME "TerraGator"  // RemoteXY connection settings 
#include <RemoteXY.h>
/**********</Dependencies>**********/



/**********<RemoteXY GUI Configuration>**********/
#pragma pack(push, 1)
uint8_t const PROGMEM RemoteXY_CONF_PROGMEM[] =   // 184 bytes V19
{ 255, 6, 0, 0, 0, 177, 0, 19, 0, 0, 0, 0, 31, 2, 106, 200, 200, 84, 1, 1,
  8, 0, 5, 6, 121, 42, 42, 41, 27, 40, 40, 32, 2, 26, 31, 2, 18, 11, 67, 23,
  2, 10, 83, 9, 1, 2, 26, 31, 31, 69, 78, 65, 66, 76, 69, 0, 75, 73, 76, 76,
  0, 2, 30, 61, 44, 22, 103, 9, 83, 9, 0, 2, 26, 31, 31, 79, 78, 0, 79, 70,
  70, 0, 129, 25, 36, 56, 6, 23, 4, 47, 5, 64, 17, 77, 111, 116, 111, 114, 32, 69,
  110, 97, 98, 108, 101, 32, 40, 82, 101, 108, 97, 121, 41, 0, 129, 30, 85, 43, 7, 127,
  2, 37, 6, 64, 17, 69, 110, 103, 97, 103, 101, 32, 66, 114, 97, 107, 101, 0, 5, 56,
  121, 42, 42, 102, 27, 40, 40, 32, 2, 26, 31, 129, 16, 166, 21, 12, 55, 70, 11, 6,
  64, 17, 76, 101, 102, 116, 0, 129, 63, 166, 28, 12, 115, 70, 14, 6, 64, 17, 82, 105,
  103, 104, 116, 0
};

// this structure defines all the variables and events of your control interface
struct {

  // input variables
  int8_t joystick_01_x; // from -100 to 100
  int8_t left_motor_y; // from -100 to 100
  uint8_t relay_sw; // =1 if switch ON and =0 if OFF, from 0 to 1
  uint8_t brake_sw; // =1 if switch ON and =0 if OFF, from 0 to 1
  int8_t joystick_02_x; // from -100 to 100
  int8_t right_motor_y; // from -100 to 100

  // other variable
  uint8_t connect_flag;  // =1 if wire connected, else =0

} RemoteXY;
#pragma pack(pop)

/**********</RemoteXY GUI Configuration>**********/



/**********<Pin Definitions>**********/
// LEDs
#define LED_1_PIN     5
#define LED_2_PIN     17
#define LED_3_PIN     16

// I2C
#define I2C_SDA_PIN   21
#define I2C_SCL_PIN   22
/**********</Pin Definitions>**********/


/**********<Macros>**********/
// LED blink rate
#define BLINK_INTERVAL      500       // toggle LED once every BLINK_INTERVAL ms

// I2C Defines
#define esp32_i2c_address   0x20
#define rp2350_i2c_address  0x40
#define I2C_FREQ            100000

// Data formatting
#define SYNC_BIT_1          0x37
#define SYNC_BIT_2          0x01
#define ROVER_CLASS_ID      0x30
#define MOTOR_SUBCLASS_ID   0x00
#define ESP32_DEVICE_ID     0x5
/**********</Macros>**********/



/**********<Global Variables>**********/
uint8_t right_motor_dir = 0;
uint8_t left_motor_dir = 0;

uint8_t left_motor_speed = 0;
uint8_t right_motor_speed = 0;

unsigned long last_toggle_time = 0;
bool led_state = false;
/**********</Global Variables>**********/



/**********<ESP32 Setup Function>**********/
void setup() {

  // RemoteXY init
  RemoteXY_Init ();

  // Serial monitor init
  Serial.begin(115200);
  delay(10);
  Serial.println("ESP32 Initializing...");

  // Initialize LEDs
  pinMode(LED_1_PIN, OUTPUT);
  pinMode(LED_2_PIN, OUTPUT);
  pinMode(LED_3_PIN, OUTPUT);

  digitalWrite(LED_1_PIN, LOW);
  digitalWrite(LED_2_PIN, LOW);
  digitalWrite(LED_3_PIN, LOW);

  // I2C init and handler setup
  Wire.begin(I2C_SDA_PIN, I2C_SCL_PIN, I2C_FREQ);
}
/**********</ESP32 Setup Function>**********/



/**********<Public Functions>**********/

/*******send_motor_commands*******
* Description
    > builds an I2C packet, transmits to RP2350 over I2C
* Arguments
    > N/A
* Returns
   > N/A
*/
void send_motor_commands(){
  // declare variables for data to transmit
      uint8_t payload[3];
      uint8_t packet[9];
      uint16_t payload_length = 3;
      
  // determine values for motor speed and direction
      if (RemoteXY.right_motor_y < 0) {
        right_motor_dir = 0;
        right_motor_speed = -1 * RemoteXY.right_motor_y;
      }
      else {
        right_motor_dir = 1;
        right_motor_speed = RemoteXY.right_motor_y;
      }
    
      
      if (RemoteXY.left_motor_y < 0) {
        left_motor_dir = 0;
        left_motor_speed = -1 * RemoteXY.left_motor_y;
      }
      else {
        left_motor_dir = 1;
        left_motor_speed = RemoteXY.left_motor_y;
      }
 

   // build payload bytes
      payload[0] = (ESP32_DEVICE_ID   << 4) |
                   (RemoteXY.relay_sw << 3) |
                   (RemoteXY.brake_sw << 2) |
                   (left_motor_dir    << 1) |
                   (right_motor_dir   << 0);

      payload[1] = left_motor_speed;
      payload[2] = right_motor_speed;

  // build header bytes
      packet[0] = SYNC_BIT_1;
      packet[1] = SYNC_BIT_2;
      packet[2] = ROVER_CLASS_ID;
      packet[3] = MOTOR_SUBCLASS_ID;
      packet[4] = (uint8_t)(payload_length & 0xFF);           // payload len LSB
      packet[5] = (uint8_t)((payload_length >> 8) & 0xFF);    // payload len MSB

  // copy payload into packet
      packet[6] = payload[0];
      packet[7] = payload[1];
      packet[8] = payload[2];

  // send packet over I2C
      Wire.beginTransmission(rp2350_i2c_address);
      Wire.write(packet, sizeof(packet));
      Wire.endTransmission();

  // lastly, return
      return;
}

/**********</Public Functions>**********/


/**********<ESP32 Loop Function>**********/
void loop() {
  // run RemoteXY handler (required)
  RemoteXY_Handler();


  // toggle LED once per 500ms
  unsigned long current_time = millis();

  if (current_time - last_toggle_time >= BLINK_INTERVAL) {
    last_toggle_time = current_time;
    led_state = !led_state;
    digitalWrite(LED_1_PIN, led_state ? HIGH : LOW);
    send_motor_commands();
    Serial.print("500ms elapsed\n\r");
  }
}
/**********<ESP32 Loop Function>**********/

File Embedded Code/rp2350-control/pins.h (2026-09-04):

#ifndef PINS_H
#define PINS_H

/******************<Summary>*****************
 * Name: pins.h
 * Purpose:
 *      > Defines values and functions for use throughout other parts of the rover code
 *      > Define values for peripheral and GPIO assignment HERE
 * Written / updated by:
 *      > Russell
******************</Summary>*****************/


/******************<Dependencies>*****************/
#include <stdio.h>
#include <stdint.h>
#include "pico/stdlib.h"

#include "hardware/i2c.h"

/******************</Dependencies>*****************/



/******************<General macros>*****************/
#define GPIO_SET_LOW            0           // for use with gpio_put
#define GPIO_SET_HIGH           1           // for use with gpio_put
/******************</General macros>*****************/



/******************<Motors>*****************/
// Motor PWM pins
#define MOTOR1_PWM              9
#define MOTOR2_PWM              8
#define MOTOR3_PWM              7
#define MOTOR4_PWM              6
#define MOTOR5_PWM              5
#define MOTOR6_PWM              4

// Motor direction pins
#define LEFT_MOTOR_CONTROL_1    3
#define LEFT_MOTOR_CONTROL_2    2
#define RIGHT_MOTOR_CONTROL_1   1
#define RIGHT_MOTOR_CONTROL_2   0

// Motor PWM Setup
#define NUM_MOTORS              6           // Number of (controllable) motors
#define PWM_WRAP                6000        // PWM wrap value (PWM period = clock_sys / wrap value)
/******************</Motors>*****************/


/******************<I2C1 Communication>*****************/
#define I2C1_BAUDRATE           100*1000    // initialize I2C at 100 kHz
#define RP2350_I2C_ADDRESS      0x40        // I2C address for this board
#define ESP32_I2C_ADDRESS       0x20        // I2C address for ESP32

// Pins
#define I2C1_SDA                10
#define I2C1_SCL                11
/******************</I2C1 Communication>*****************/


/******************<Safety Devices>*****************/
// Relay pins
#define RELAY_CONTROL           39
#define RELAY_FB                38

// LEDs
#define LED_1_PIN               21
#define LED_2_PIN               20
#define LED_3_PIN               19
#define LED_4_PIN               18
#define LED_5_PIN               17
/******************</Safety Devices>*****************/


#endif // PINS_H

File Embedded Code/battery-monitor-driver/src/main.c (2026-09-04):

#include <stdio.h>
#include <unistd.h>
#include "pico/stdlib.h"
#include "hardware/spi.h"
#include "hardware/i2c.h"
#include "hardware/uart.h"
#include "hardware/adc.h"
#include "board_config.h"
#include "drivers/current_sens.h"
#include "drivers/voltage_sens.h"
#include "drivers/sseg.h"
#include "drivers/status.h"
#include "drivers/payload.h"

int main()
{
    // initialization procedures 
    board_config();  
    sseg_init(); 
    voltage_sens_init(); 
    // current sens is just ADC, which is configured in board_config();
    led_init();
    // initialize running average filter
    struct runningAverageFilter current_filter;
    struct runningAverageFilter voltage_filter; 
    running_average_init(&current_filter); 
    running_average_init(&voltage_filter); 

    // ADDITIONS BEGIN HERE
    
    // TO-DO : fill this in with our battery parameters!
    BatteryConfig config = {
        .cell_count = 0, // [Cells]
        .capacity_mAh = 0, // [mAh]
        .max_voltage = 0.0f, // [V]
        .min_voltage = 0.0f, // [V]
        .max_discharge_current = 0.0f, // [A]
        .max_charge_current = 0.0f, // [A]
        .expected_current = 0.0f, // [A]
    };
    set_battery_config(config);
    // Sending battery config once upon startup
    send_battery_config_payload();
    // ADDITIONS END HERE
    
    //printf("Beginning serial output..."); 

    // small delay before beginning to read to allow initializations time to settle 
    sleep_ms(10);
    while(1)
    {
        // get voltage and current data 
        float raw_voltage = read_bus_voltage(); 
        float raw_current = get_current_sens_reading(); 
        float filtered_voltage = running_average_update(&voltage_filter, raw_voltage);
        float filtered_current = running_average_update(&current_filter, raw_current); 
        
        /* serial outputs for debugging. Commented for future debugging use
        printf("Voltage reading: %f\n", raw_voltage); 
        printf("Current reading: %f\n", raw_current);
        printf("Filtered voltage: %f\n", filtered_voltage); 
        printf("Filtered current: %f\n", filtered_current);
        printf("--RA current structure attributes--\n"); 
        printf("val_count, %d\t", current_filter.val_count); 
        printf("index, %d\t", current_filter.index);
        printf("sum, %f\n", current_filter.sum); 
        printf("--RA voltage structure attributes--\n"); 
        printf("val_count, %d\t", voltage_filter.val_count); 
        printf("index, %d\t", voltage_filter.index);
        printf("sum, %f\n", voltage_filter.sum); 
        */
       
        // output voltage and current values to LED driver over SPI every ~100 ms
        sleep_ms(100); 
        max7219_voltage_current_write(filtered_voltage, filtered_current); 

        // update status LEDs onboard battery monitor
        uint8_t status = change_led_indicators(filtered_voltage, filtered_current);
        
        // sending every ~100 ms using according to MIL UART 
        send_payload(status, filtered_voltage, filtered_current);
    }
}

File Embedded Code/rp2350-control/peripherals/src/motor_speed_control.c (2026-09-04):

/******************<Dependencies>*****************/
#include "peripherals/motor_speed_control.h"
/******************</Dependencies>*****************/


/******************<Private variables>*****************/
bool motors_initialized = false;           // keeps track of whether or not initMotors has been called
char current_motor_mode = ' ';             // keeps track of motor mode (only updated when mode for both sides is updated)
/******************</Private variables>*****************/


/******************<Public variables>*****************/
motor_str motors[NUM_MOTORS];               // Global array of motor structs
/******************</Public variables>*****************/


/******************<Function definitions>*****************/

/*******init_motors*******
 * Description
        > initializes all motor PWM stuff
 * Arguments
        > N/A
 * Returns
        > N/A
*/
void init_motors() {

    // First, set GPIO pins for each motor
        motors[0].motor_ID = 1;                         // Motor #1
        motors[0].side = 0;                             // left side of rover
        motors[0].GPIO_pin = MOTOR1_PWM;

        motors[1].motor_ID = 2;                         // Motor #2
        motors[1].side = 0;                             // left side of rover
        motors[1].GPIO_pin = MOTOR2_PWM;

        motors[2].motor_ID = 3;                         // Motor #3
        motors[2].side = 0;                             // left side of rover
        motors[2].GPIO_pin = MOTOR3_PWM;

        motors[3].motor_ID = 4;                         // Motor #4
        motors[3].side = 1;                             // right side of rover
        motors[3].GPIO_pin = MOTOR4_PWM;

        motors[4].motor_ID = 5;                         // Motor #5
        motors[4].side = 1;                             // right side of rover
        motors[4].GPIO_pin = MOTOR5_PWM;

        motors[5].motor_ID = 6;                         // Motor #6
        motors[5].side = 1;                             // right side of rover
        motors[5].GPIO_pin = MOTOR6_PWM;

    // Second, set configuration for PWM pins
        pwm_config config = pwm_get_default_config();   // get default PWM configuration
        pwm_config_set_clkdiv(&config, 4.f);            // set divider, reduces counter clock to sysclock/this value

    
    // Third, run for loop to initialize each motor PWM slice & channel
        uint8_t initialized_slices[NUM_MOTORS];
        bool slice_initialized = false;

        for (uint8_t i = 0; i < NUM_MOTORS; i++){
            initialized_slices[i] = 100;                // Set all values of this array to something other than 0. Prevents Slice 0 from going uninitialized.
        }

        for (uint8_t i = 0; i < NUM_MOTORS; i++){
            // i: set GPIO pin to be PWM
                gpio_set_function(motors[i].GPIO_pin, GPIO_FUNC_PWM);

            // ii: get slice and channel for this pin
                motors[i].PWM_slice   = pwm_gpio_to_slice_num(motors[i].GPIO_pin);
                motors[i].PWM_channel = pwm_gpio_to_channel(motors[i].GPIO_pin);      // 0=A, 1=B

            // iii: initialize slice, or skip if this slice has already been initialized
                slice_initialized = false;

                for (uint8_t j = 0; j < NUM_MOTORS; j++){   // check if this slice has been initialized
                    if (initialized_slices[j] == motors[i].PWM_slice){
                        slice_initialized = true;
                        break;
                    }
                }

                if (slice_initialized == false){            // initialize slice if not yet initialized
                    pwm_config_set_wrap(&config, PWM_WRAP);
                    pwm_init(motors[i].PWM_slice, &config, true);
                }
        }

    // Fourth, initialize control logic pins
        gpio_init(LEFT_MOTOR_CONTROL_1);                    // initialize pins
        gpio_init(LEFT_MOTOR_CONTROL_2);
        gpio_init(RIGHT_MOTOR_CONTROL_1);
        gpio_init(RIGHT_MOTOR_CONTROL_2);

        gpio_set_dir(LEFT_MOTOR_CONTROL_1, GPIO_OUT);       // set control logic pins as outputs
        gpio_set_dir(LEFT_MOTOR_CONTROL_2, GPIO_OUT);
        gpio_set_dir(RIGHT_MOTOR_CONTROL_1, GPIO_OUT);
        gpio_set_dir(RIGHT_MOTOR_CONTROL_2, GPIO_OUT);

    // Fifth, indicate that initMotors() has been run
        motors_initialized = true;

    // Sixth, print debug message
        printf("Motors initialized\n");
}


/*******printMotorDetails*******
 * Description
        > prints out information about each motor's PWM settings
 * Arguments
        > N/A
 * Returns
        > N/A
*/
void printMotorDetails() {

    // Prepare variables for this function
        uint8_t ID = 0;
        uint8_t side = 0;
        uint8_t GPIO_pin = 0;
        uint8_t slice = 0;
        uint8_t channel = 0;

        char side_ch = ' ';
        char channel_ch = ' ';

    // Print motor data
    printf("*****Printing motor PWM settings*****\n");

    for (uint8_t i = 0; i < NUM_MOTORS; i++){

        // i: get data from motor struct
            ID          = motors[i].motor_ID;
            side        = motors[i].side;
            GPIO_pin    = motors[i].GPIO_pin;
            slice       = motors[i].PWM_slice;
            channel     = motors[i].PWM_channel;

        // ii: format data as needed
            if (side == 0){side_ch = 'L';}
            else {side_ch = 'R';}

            if (channel == 0){channel_ch = 'A';}
            else {channel_ch = 'B';}
            
        // iii: print data for this motor
            printf("\t> Motor %u\n", ID);
            printf("\t\t- Side: %c\n", side_ch);
            printf("\t\t- GPIO: %u\n", GPIO_pin);
            printf("\t\t- PWM Slice: %u\n", slice);
            printf("\t\t- PWM Channel: %c\n", channel_ch);

    }
}
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

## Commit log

2025-09-19 09/19 Commit
    I'll be clearing Windows from my laptop, backing up all repos I'm working in.
    [Battery Monitor V1.PrjPcb, Devices.SchDoc, Interface Board V0.PrjPcb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]
2025-09-23 small tof board
    Basic starting board for ToF sensor. May need to add a level shifter and voltage regulation depending on how we want to configure the interface board.
    [ToF_Sensor_Breakout_v1.PrjPcb, main.PcbDoc, main.SchDoc]
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2025-09-24 Revision 0 of ToF board
    First full board complete.
    [ToF_Sensor_Breakout_v1.PrjPcb, main.PcbDoc, main.SchDoc]
2025-09-25 minor changes to ToF board
    Should be finalized design, barring any changes after full review
    [main.PcbDoc, main.SchDoc]
2025-09-25 Reworked board because I missed a route (-_-)
    Also changed to the sensor I used to test ToF in the lab. I initially thought they were out of stock but I was wrong.
    [main.PcbDoc, main.SchDoc]
2025-09-26 Rotated board and changed sensor
    Rotated board and changed sensor to the one I tested earlier in the lab. Wanted to use this one initially but thought it was out of stock.
    [ToF_Sensor_Breakout_v1.PrjPcb, main.PcbDoc]
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2025-09-29 09/29 - Cleaning up repo
    many changes
    [0_5_in_shaft.SLDPRT, 0_75_in_shaft.SLDPRT, 35362-0450.SchLib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]
2025-09-29 moved some files around
    [0_5_in_shaft.SLDPRT, 0_75_in_shaft.SLDPRT, 3_in_pin.SLDPRT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]
2025-09-29 deleted everything except ToF board
    [BOM.xlsx, Battery Monitor V1.PrjPcb, Battery Monitor.PrjPcb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]
2025-09-29 Pulling everything from ToF into main
    [ToF_Sensor_Breakout_v1.PrjPcb, main.PcbDoc, main.SchDoc]
2025-10-02 Updates on Interface Board
    [CubePilot and Motor Drivers.SchDoc, I2C Connections.SchDoc, Interface Board V0.PrjPcb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]
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2025-10-08 Added designators to BOM
    [BOM_ToF_board.xlsx]
2025-10-08 Generated production files for ToF and Interface PCBs
    [Interface Board V0.PrjPcb, ToF_Sensor_Breakout_v1.PrjPcb, main.PcbDoc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]
2025-10-09 Completed Interface Board V0 BOM
    [BOM - Interface Board V0.xlsx, CubePilot and Motor Drivers.SchDoc, Interface Board V0.PrjPcb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]
2025-10-09 ugh more changes
    - added poly pour on top and bottom layer for Interface Board
    [Interface Board V0.PrjPcb, main.PcbDoc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]
2025-10-09 moved USB port on Interface Board to avoid collision with Raspberry Pi
    [main.PcbDoc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]
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2025-10-15 Started work on Pi Control Board / Interface Board V1
    [ESP32-S2.SchDoc, Motor Drivers.SchDoc, NRF24L01P.SchDoc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]
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2025-10-23 Beat the compilation errors
    [main.c]
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2025-10-27 Finished schematic for distance sensor interface board and updated ToF breakout schematic
    [Distance-Sensor-Board.PrjPcb, Distance-Sensors.SchDoc, MCU.SchDoc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]
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2025-10-30 Fixed some bugs in the code
    Fixed some bugs and completed the led/status indication logic. Will test this code tomorrow and hopefully will have battery monitor fully programmed before the weekend.
    [main.c]
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2025-11-03 minor changes
    These changes should hopefully fix the erroneous outputs I was reading from the board on Friday
    [main.c]
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2025-11-07 Finished 3v3->1v8 level shifter board
    This board will be used to test our current ToF sensors to ensure proper connections.
    [Distance-Sensors.SchDoc, ToF-Level-Shifter-Breakout.PrjPcb, main.PcbDoc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]
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2025-11-17 3v3 <-> 1v8 bidirecitonal level-shifter
    Made a level-shifting breakout board for testing soldering practices and confirming i2c communications with our ToF sensors.
    [ToF-Level-Shifter-Breakout.PrjPcb, main.PcbDoc, main.SchDoc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]
2025-11-17 Worked some more on distance sensor layout
    Continued to follow the RP2350 hardware design manual while also referencing a minimal PCB design provided by Raspberry Pi.
    [main.PcbDoc]
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2025-11-22 Finished first full wiring of distance sensor board
    First full wiring for the board is done. I'm not super happy with the wiring setup I have going for the ToF sensor group (i2c lines, level shifter, shutdown pins, etc.), and I think I came up with a 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
    [Distance-Sensor-Board.PrjPcb, Distance-Sensors.SchDoc, MCU.SchDoc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]
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2025-11-23 First version of the distance sensor board complete
    I completed the first version of the distance sensor board. Will probably write a wiki page for it soon,
    [Distance-Sensors.SchDoc, MCU.SchDoc, main.PcbDoc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]
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2025-11-24 Added BOMs for distance sensor and breakout boards
    Also made small change to the distance sensor's 5V polygon pour.
    [Distance-Sensor-Board-BOM.xlsx, ToF-Level-Shifter-Breakout-BOM.xlsx, main.PcbDoc]
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2025-11-27 lots of updates!
    - got esp32 talking to rp2350 over I2C
    - set up a GUI to run on a phone using RemoteXY (thanks Jeremiah!)
    - got basic drive forward/backward/neutral/brake functionality working
    - accidentally blew up a buck converter while testing on rover :(
    - need to work on tank-style turning next
    - gonna work on PCBs for a bit
    [esp32-code.ino, motor_speed_control.c, rover_cli.c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]
2025-12-01 minor silkscreen change to label boot and run buttons for pico
    [main.PcbDoc]
2025-12-01 work done on pcbs
    - largely completed pi control board, need to switch SMA connectors to RP-SMA for 2.4 GHz operation
    - rover power board is still work in progress
    [ESP32-S2.SchDoc, Misc.SchDoc, Motor Drivers.SchDoc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]
2025-12-02 Hopefully finished PCB layout for Rover Power Board
    [Power Connections.SchDoc, Rover Power Board V0.PrjPcb, Servo Level Shifter.SchDoc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]
2025-12-04 pcb work
    - started V2 of Battery Monitor, decided to postpone reordering it because the board has some serious design errors that require more time/attention than I can give now, the existing V1 board in the lab will work and is repairable, but serious design work must be done on my earlier version of the board before it should be reordered
    - still need to switch out the SMA connectors on the Pi Control Board to be RP-SMA to account for 2.4 MHz operation
    [Battery Monitor V2.PrjPcb, Battery Monitoring.SchDoc, DC Step-Down Converter.SchDoc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]
2025-12-04 generated fabrication files for 3 boards
    - Pi Control Board V0
    - Rover Power Board V0
    - Rover Safety Board V0
    [ESP32-S2.SchDoc, NRF24L01P.SchDoc, Pi Control Board V0.PrjPcb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]
2025-12-04 generated fabrication files for Distance Sensor Board V0
    [Distance-Sensor-Board.PrjPcb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]
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2025-12-22 pcb work
    had some assembly issues with pi control. Apparently, cramming as many components as you can into a small area makes it hard to find shorts :(
    instead of spending many more hours fixing that, I'm separating each subsystem onto its own small, cheap, easily-debuggable pcb. the goal is to not pull all my hair out
    [Connections.SchDoc, ESP32-S2.SchDoc, ESP32.SchDoc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]
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2026-02-03 moved all pcb files into the right place
    [BOM_ToF_board.xlsx, Connections.SchDoc, Distance-Sensor-Board-BOM.xlsx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]
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2026-02-17 Minor fixes to Rover Power Board (V1 -> V2)
    [Main.PcbDoc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]
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2026-03-30 March 29th Update
    Moved the send_payload() function to a proper .c and .h file.
    Added additional functionality to allow future use of sending, setting, and getting the current battery configuration allowing for the following parameters:
    cell_count, capacity_mAh, max_voltage, min_voltage, max_discharge_current, max_charge_current, expected_current
    The last few may be a bit redundant as there's times we may not be drawing much current or clearly not sending data while charging, but as a baseline it couldn't hurt to add.
    Will confirm this was the expected result with Aiden. likely not proper or correct on the first try, but that's what I'm here for!
    ☕
    [main.c, payload.c]
2026-05-31 5/31 ultrasonic distance sensor board done 👍
    The purpose of this board is for connecting the Ultrasonic Distance Sensors to the exterior of the Rover. It also changes the connection from a dupont to a sherlock.
    [Ult_Sonic_main.PcbDoc, Ult_Sonic_main.SchDoc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]
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
